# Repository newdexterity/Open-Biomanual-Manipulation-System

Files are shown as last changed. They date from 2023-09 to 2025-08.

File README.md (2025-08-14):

# The New Dexterity Open-Source Bimanual Manipulation Platform (OpenBMP) for Education and Research
Open Source Anthropomorphic Bimanual Manipulator Robot project initiated by New Dexterity

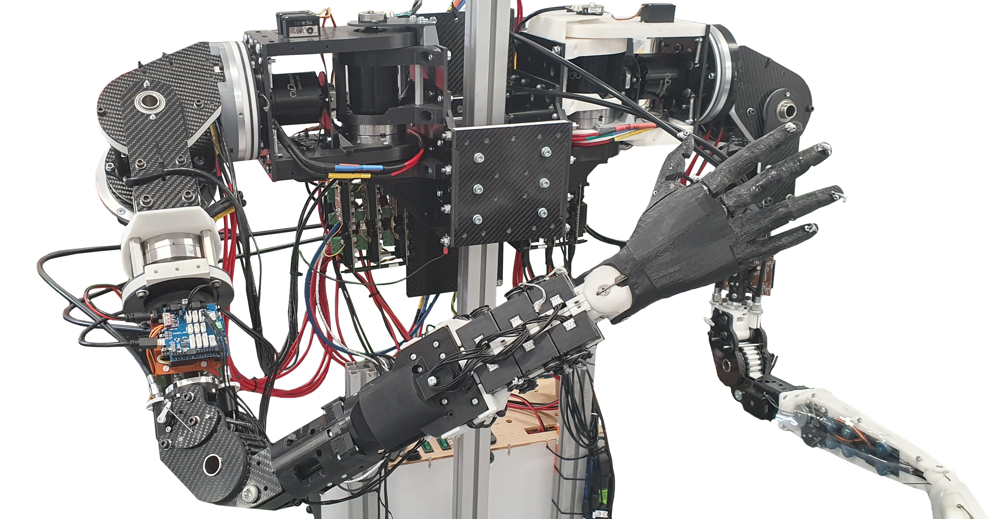
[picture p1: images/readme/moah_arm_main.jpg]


# Related Publications

[ICRA 2024 - Overview and tele-manipulation](https://www.researchgate.net/publication/380467006_The_New_Dexterity_Modular_Dexterous_Anthropomorphic_Open-Source_Bimanual_Manipulation_Platform_Combining_Adaptive_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)
[tASL paper]()

## Repository Contents
This repository contains the following material:

* Assembly guide folder - [Wiki](../../wiki)
* CAD folder - Design files of the bimanual platform for manufacturing
* Software folder - Interface for joint control - WIP (Sorting through code)

### Folder Directory
    .
    ├── ..
    ├── Assembly guide
    │   ├── Bill_of_Materials.xlsx               # Bill of Materials (WIP)        
    │   └── README.md
    ├── CAD                                      # Software folder for various subsystems
    │   ├── ...                                  
    │   ├──                                      # Various submodules of the OpenBMP system
    │   ├── ...   
    │   ├── README.md
    │   └── open_bmp_asm.7z                      # Assembled robot CAD
    ├── Software                                 # Software folder for various subsystems
    │   ├── Arduino_ESP32                        # Arduino code for operating the forearm and human-like hands for the ESP32
    │   ├── CaptoGloveDocker                     # Captoglove Docker scripts for installing and interfacing with ROS (Bluetooth)
    │   ├── Odrive_Settings                      # ODrive sample settings for setting up the ODrives (WIP)
    │   ├── moah_src                             # Main package for simulation, visualization, and operation of the robot
    │   ├── pi_catkin_ws_src                     # Code for the RPi4 CAN passover module and setup of the RPi4 for multimachine ROS
    │   │   ├── config.txt                       # RPi4 config for SPI bridge to CANBUS controller
    │   │   ├── syscfg.txt                       # RPi4 config for SPI bridge to CANBUS controller
    │   │   └── usercfg.txt                      # RPi4 config for SPI bridge to CANBUS controller and hdmi output settings
    │   ├── README.md                            # *** Overview readme file ***
    │   └── Screenshot 2023-10-12 15_46_23.png
    ├── LICENSE
    └── README.md

# About the Modular Open-source Arm Hand (MOAH) Hybrid-drive Bimanual Arm Hand System
## The Mission

The modular, dexterous, anthropomorphic Open-source Bimanual Manipulation Platform (OpenBMP) is a collaborative open-source robot manipulator project initiated by the New Dexterity group aimed to provide a low-cost research platform for studying bimanual manipulator systems and experimental actuating systems or kinematic configurations. It follows the footsteps of ARoA, a humanoid Autonomous Robotic Assistant.

OpenBMP consists of two Modular Open-source Arm Hand (MOAH) manipulators, a single-arm manipulator system designed for simple fabrication and catering to different end effectors and forearm modules.

## System Overview
The system utilizes rapid prototyping technologies such as FDM printing and waterjet cutting to manufacture robust custom parts through carbon fiber plate-reinforced 

The bimanual platform is equipped with a pair of modular, 5 DoF upper, mixed-drive manipulators with four axially driven joints and one tendon-driven joint in each arm. A 1:100 reduction harmonic drive from HanZhen Technology was used in each direct axial drive joint, enabling standard connectors between the various modules. The Bowden cable tendon-driven elbows allow the actuating mechanism to be placed away from the joint, reducing the arm's inertial moments. Each upper arm shoulder unit joint is driven by a dual shaft brushless DC (BLDC) motor, the D6374-150KV, from ODrive robotics. The position feedback employs absolute encoders, AMT232B-V from CUI Devices, to provide compact, accurate, and fast position controls. The torso structure was designed to be mounted on a pair of opposing linear rails to access a larger reachable workspace similar to the variable torso of the New Dexterity ARoA humanoid. 

* Lightweight and reconfigurable structure
* Bowden drive joints
* Box-style structure for easy access and maintenance
* Open-source ODrive Controllers for BLDC motors

## Robot Hardware Overview

### Foldable Shoulder
The foldable shoulder enables re-orientation of the manipulator bases, allowing for a larger intersecting bimanual workspace. This demonstrates how the modular platform can be modified for different kinematic designs through different actuator orientations. With detachable modules and 3D-printed sandwiched plate structures, the layout of the system can be quickly reconfigured. For example, a raised shoulder abduction module can be used to fit different types of robotic configurations and designs. 

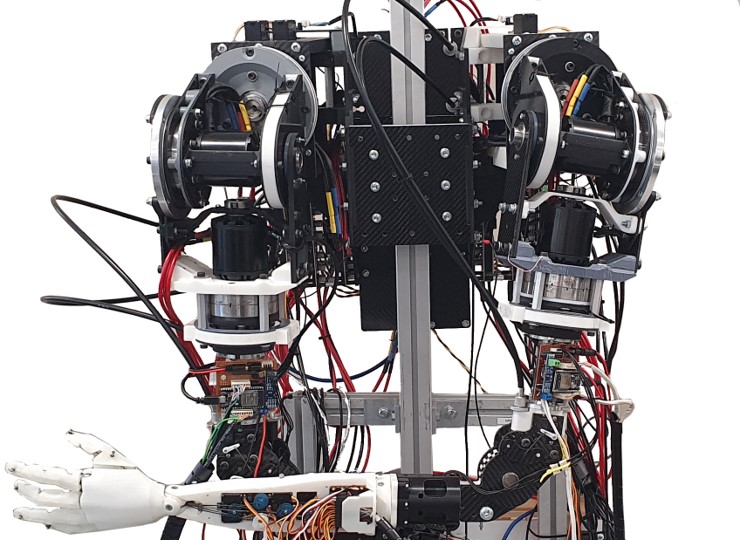
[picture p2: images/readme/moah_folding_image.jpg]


### Joint Locking
A specialized joint locking mechanism is used in both the shoulder and elbow flexion joints, mitigating motor stress during high-load manipulation tasks such as holding extended poses for long periods. The ratchet lock systems employed enable the joints to maintain their position with minimal energy expenditure, thereby reducing the overall torque exerted on the motors. The curved design also allows gravity-assisted locking modifications for future iterations.
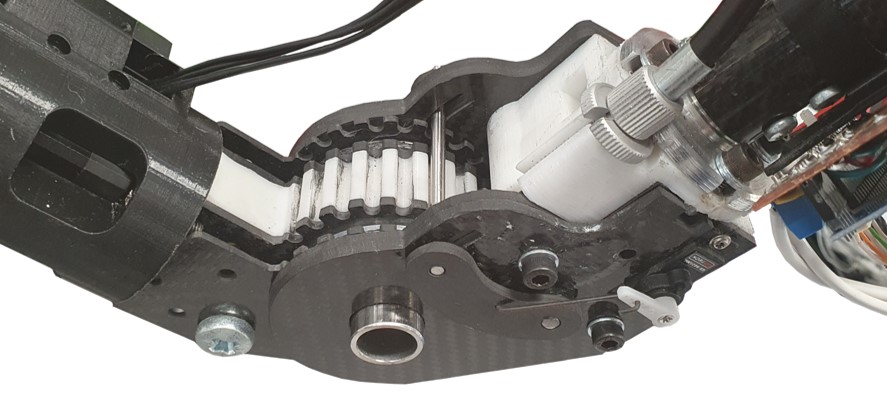
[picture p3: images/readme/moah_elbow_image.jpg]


### Low-inertial Manipulators and Experimental Transmissions
The system incorporates two types of reducer transmission mechanisms that were used to demonstrate the versatility and capability of the platform. One is a directly coupled tendon drive onto the harmonic drive output with a total reduction of approximately 61.17. The other is a simple pulley system routed around central idler wheels for the compactness of a single-joint drive. The pulley system consists of an antagonistic 1:6 reduction pulley set with an output tendon driver reduction of 2.6. The total reduction is approximately 15.6. Both transmission systems use Bowden cables to route the tendons to the elbow joint and are fitted with in-line cable tensioners. The design enables easy exchange or modification of the elbow module without disassembling the shoulder modules and also allows for the replacement of Bowden cable sets through slotted in-line cable tensioners without requiring disassembly of the robot. 

## The Design

The torso and bi-manual upper arm unit were constructed using 3D printed polylactic acid (PLA) high-strength filament parts, which were reinforced with carbon fibre composite plates in regions subjected to high loads. This choice of materials enables rapid prototyping and facilitates easy design modifications via Fused Deposition Modeling (FDM) 3D printing and waterjet cutting. The rigidity of the carbon fibre plates prevents structural deformation of the PLA parts, and the conductive nature provides grounding planes in the chassis. Additionally, certain modules were structurally reinforced using aluminium standoffs, and a machined keyed shaft adapter drove each motor-harmonic drive module.

Here is an overview of the structural parts required for assembling the torso and one of the upper arm units:
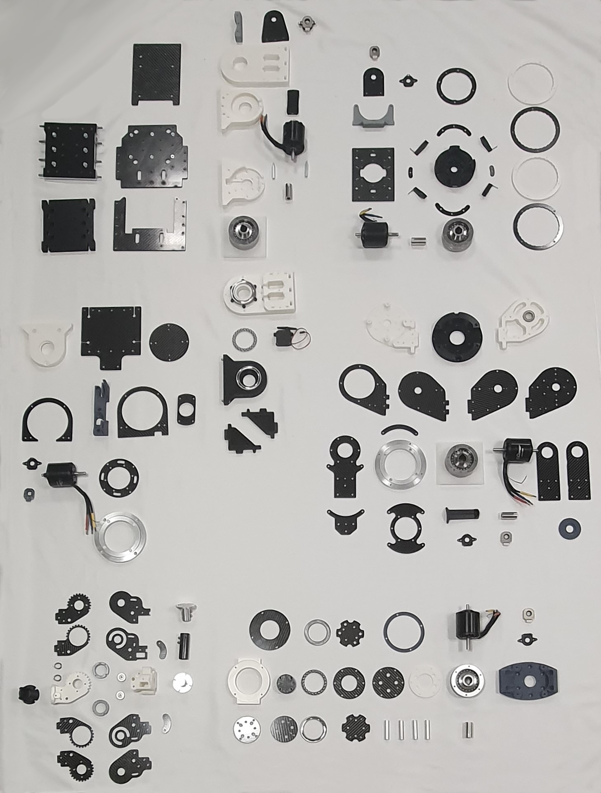
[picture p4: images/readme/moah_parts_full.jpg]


### Torso Base Unit
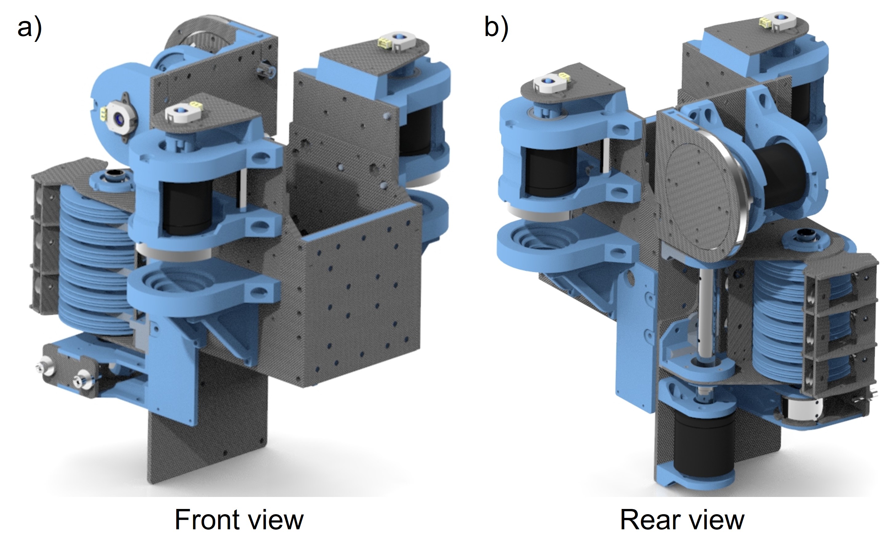
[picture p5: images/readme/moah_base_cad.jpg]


### Torso Clavicle Unit
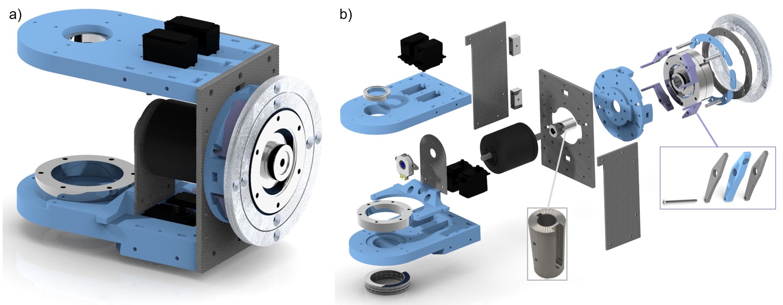
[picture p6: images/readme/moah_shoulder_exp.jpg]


### Shoulder Unit
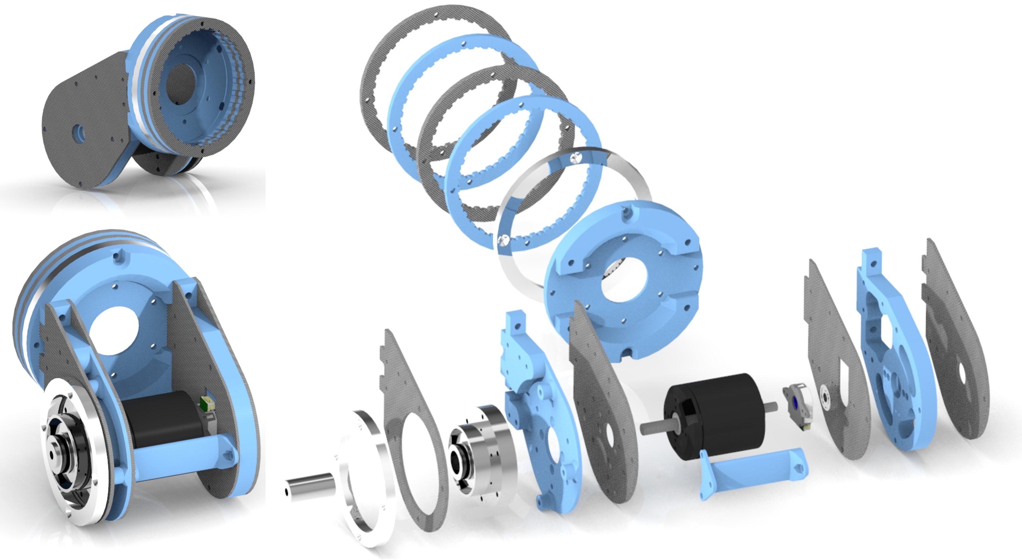
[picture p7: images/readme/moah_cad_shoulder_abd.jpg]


### Shoulder Rotation Unit
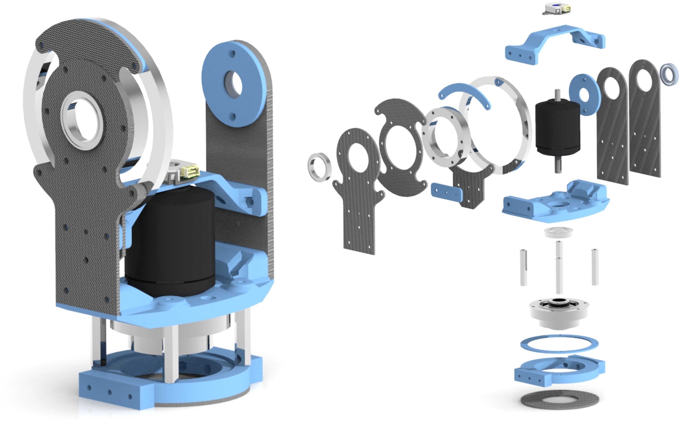
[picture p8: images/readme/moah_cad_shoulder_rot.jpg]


### Elbow Unit
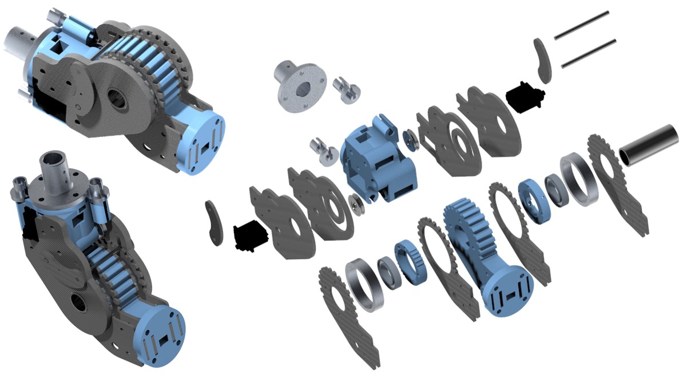
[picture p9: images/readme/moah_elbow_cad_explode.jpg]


### Forearm Modules
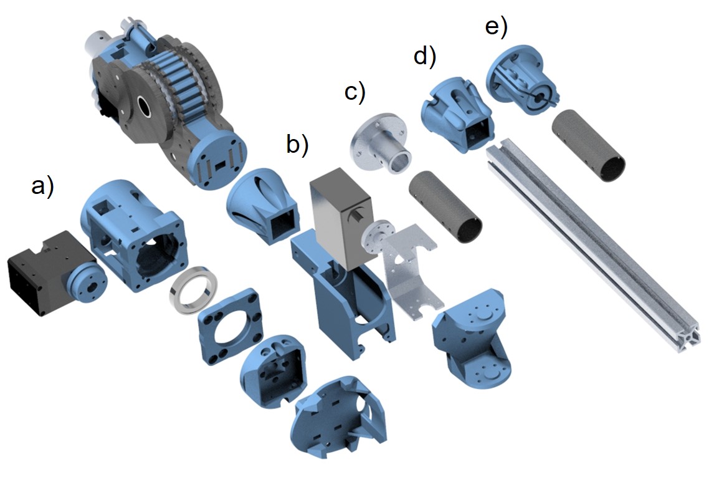
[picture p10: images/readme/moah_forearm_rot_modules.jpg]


### Wrist/Hand Modules
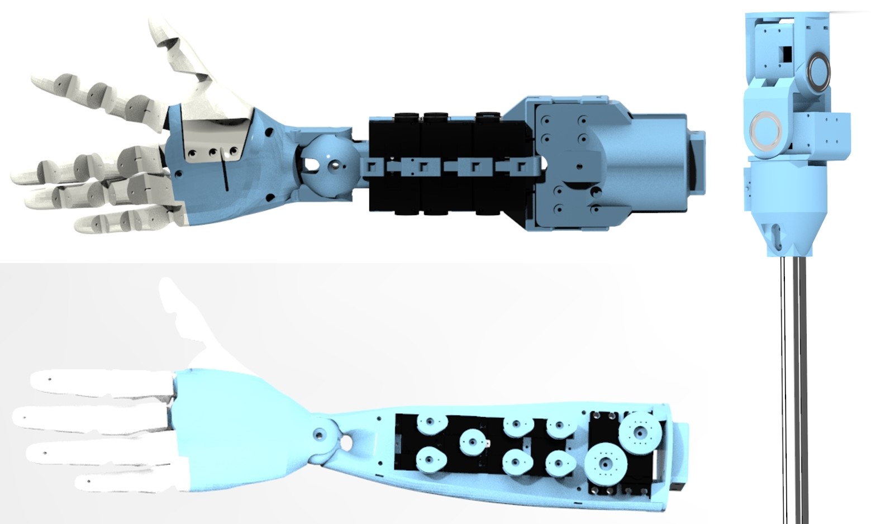
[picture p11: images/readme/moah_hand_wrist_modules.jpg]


## Robot Manipulator specifications
* Reachable arm length: 1000 mm
* Single arm weight: 12.4 kg 
* Software requirements: ROS Melodic/Noetic
* Multimachine communication: Ethernet via router
* CAN bus communication: CANbus hat via SPI with RPi4 using ROS noetic for arm64
  
### Hardware costs (approximate) (USD):
>    ### Bimanual robot arm platform (without forearm module):
>         $11600
>    ### Single ASL hand (servo Ver.)
>         $450
>    ### Single Dynamixel hand
>         $1920
>    ### Single unit of robotic wrist module
>         $1230

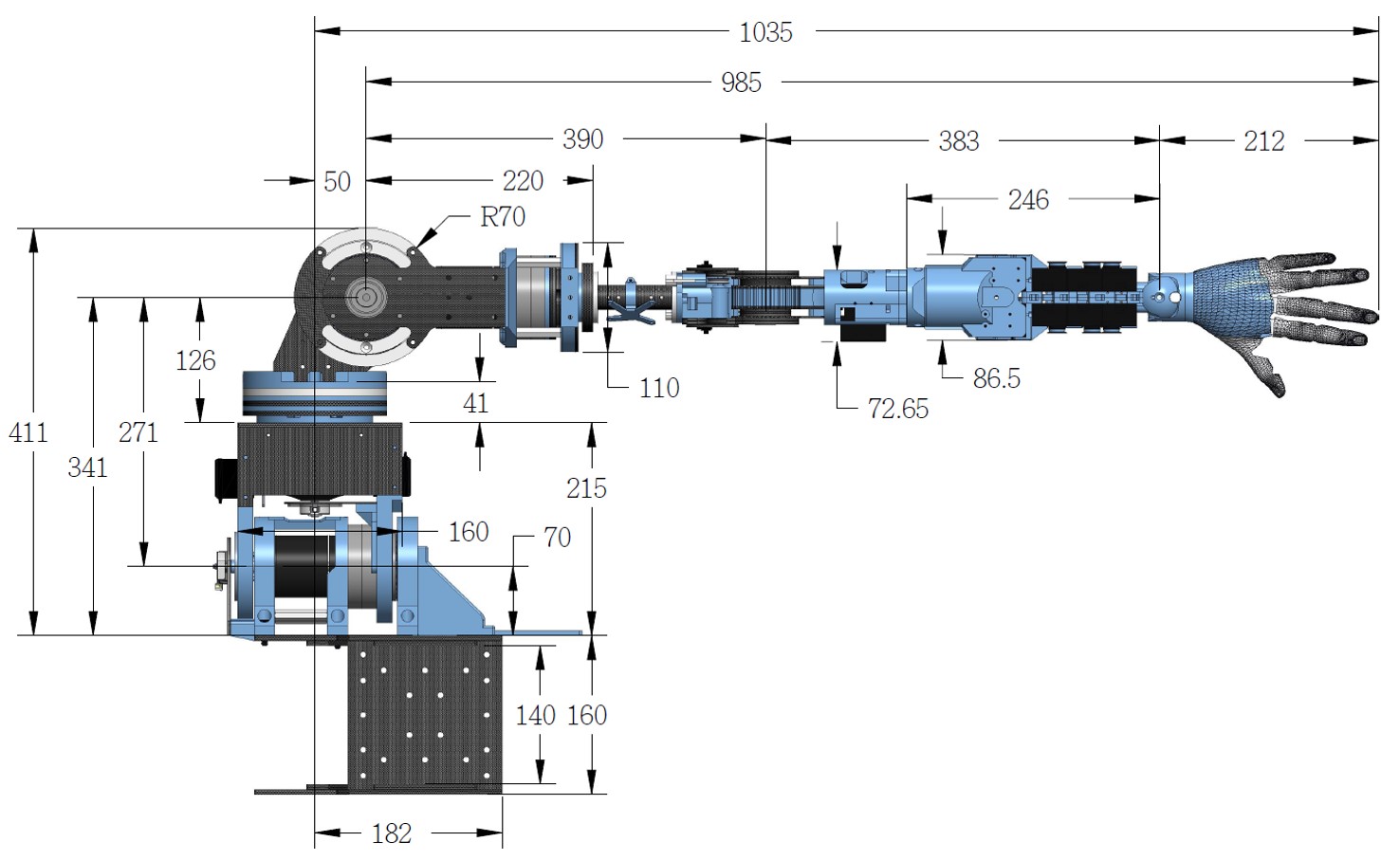
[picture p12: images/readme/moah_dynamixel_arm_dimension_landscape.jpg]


### Theoretical capabilities:
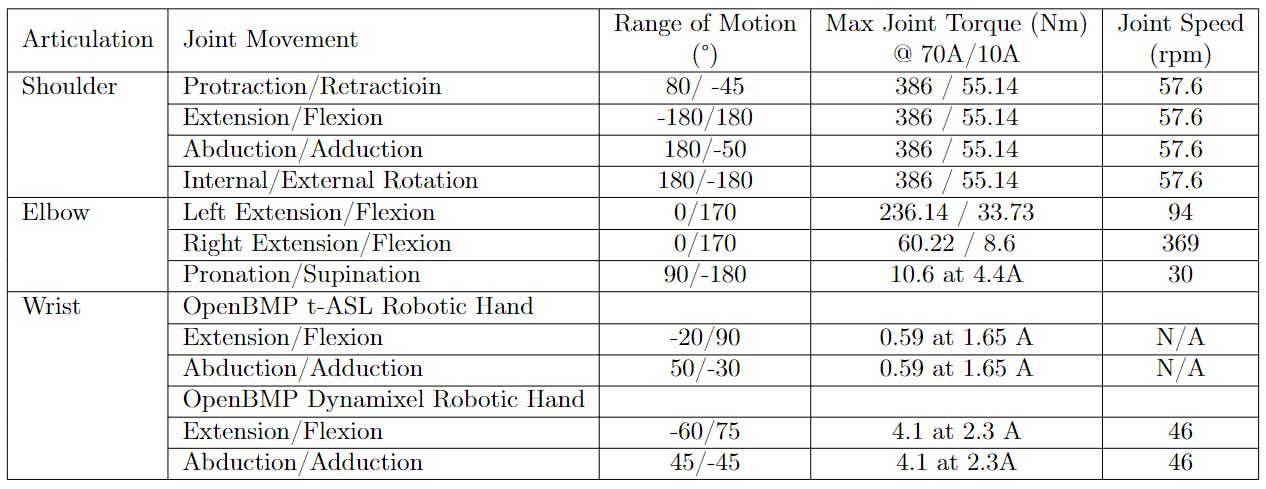
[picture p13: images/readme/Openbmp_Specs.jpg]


## Computer and Electronics

* Robot CAN controller node: Raspberry Pi 4 Model B with custom MCP2515 CAN controller and MCP2551 CAN transceiver hat
* Main Computer: Intel NUCi7 or similar with Ubuntu 18.04 with ROS melodic - 20.04 noetic should work
* Router: TP-link Archer VR300 (any router would do)
* Power supplies: assorted 6V, 12V, 24V or 48V power supplies
* Microcontrollers: ESP32 boards for ROS control for forearms and hands
* MAX485 transceiver boards for RS485 communication with Dynamixel motors
* Vero boards for custom interfacing
* Tri-state buffer (74AHC1G125S) for AMT232 SPI communication with ODrive
* Old Ethernet cables for signal wiring
* Assorted cables for power wiring

## Teleoperation
The robot can accept a variety of input controls via the ROS framework. The base system demonstrates the integration of different telemanipulation controllers with the Captoglove and the Polhemus magnetic system.

## Power Distribution System - WIP
The 56V ODrive controllers can operate motors with voltages up to 56V and peak currents of 120A per motor. However, for continuous operation, it is recommended to operate at a much lower current.

Heatsink only in still air: 40A
Heatsink with basic fan cooling: 75A
Heatsink with overkill fan cooling: 90A

Retrieved from :
[Details](https://discourse.odriverobotics.com/t/odrive-mosfet-temperature-rise-measurements-using-the-onboard-thermistor/972)

The base system limits current supply at 10A and voltage at 24V for safety in testing and operation. A higher current and voltage bypass is possible via the optional 48V battery pack. 
Here's a link to a nice article on power source selection:
[Details for custom powersources](https://things-in-motion.blogspot.com/2018/12/how-to-select-right-power-source-for.html)

## Endpoint Traverse Speed - WIP
The motors were limited to 60rpm on the ODrive controller, which is roughly 6 rpm after the harmonic reducers. Using the DH parameter and Jacobian, the end traverse speed is about 0.27m/s.
This was both a structural safety precaution as well as the power system limit. However, from experiments, the system did reach speeds of 0.36m/s during motion replication tasks.
If we use the theoretical max speed per joint, of 57.6 rpm, this computes to about 2.59m/s. The system has not been stress-tested at this kind of speed!

https://github.com/adam-p/markdown-here/wiki/Markdown-Cheatsheet

https://github.com/orgs/community/discussions/16925

<p align="justify"> The project is distributed under the Creative Commons Attribution-NonCommercial 4.0 International (CC BY-NC 4.0) </p>

[CC BY-NC 4.0](https://creativecommons.org/licenses/by-nc/4.0/)

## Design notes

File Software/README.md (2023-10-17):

# Software:
All the software needed to run MOAH is organized in this folder.

# WIP:

- [ ] Organize the code
- [ ] Replicate the code in a fresh system
- [ ] Implement low-level CAN-Bus communication directly from the ROS Control driver

<!---
# RIS for RPi4
Please follow the link to install ROS-noetic on RPi4. Steps for custom configurations such as boot-previlages, network settings, SPI settings, and setup of the RPI4 is currently a WIP.

# moah_ws

Example ROS interface to control the bimanual manipulator system. Modular, Open-source Arm Hand (MOAH) system was the old project name.
This includes the simulation and operation of the robot in rViz.

## Dependencies

# CaptoGloveDocker

The Bluetooth communication is set within a docker and can be installed following the steps listed below :

* WIP

## Setting Up ODrive Controllers
Please make sure to go through [getting started](https://docs.odriverobotics.com/v/0.5.6/getting-started.html) page for setting up and tuning the ODrive motors
A set of basic initial settings is avaliable for the ODrives

### Setting commands and motor numbering

## System Networking

You will need some ethernet cables, a router, a computer (our case was the NUC7), and a RPi4. 

### Main Computer (with moah_ws)

```
ROS_MASTER =
```

```
ROS_IP =
 ```
### RPi4 ROS to CANbus Passover

```ROS_MASTER = ```
```ROS_IP = ```

## Virtual Interface Usage
### On the Main Computer (with moah_ws)
* ToDo - add a screenshot of the terminator split screen
First start rescore

```
roscore
```

Then, run the following command to bring up the visualizer.

```
roslaunch
```

If you wish to test the robot model, edit the `view_arm.launch` files and uncomment the GUI controls for slider control of the robot arms

To bringup the controllers, run the following

```
roslaunch
```

To start the motion remapping via functional anthropomorphism, run the following commands to start the controller for each of the arms.

```
roslaunch
```

```
roslaunch
```

### Connection to Input Interfaces
The robot system is designed for the hybrid glove setup with individual controls for the hand and arm. 
The Captoglove bluetooth interface is setup within a Dockerfile. 

If the Captoglove is not showing blue, (most likely orange or magneta) press and hold the button until an orange light flashes after the light turns off (approx, 9 secs). This should set the captoglove into a white light indicator for it to be in pairing mode.

change your directory to the installed docker folder
```
cd CaptoGloveDocker
```

start docker

```
./start melodic_11
```

make sure dbus connection is successful

#### Connecting Captoglove
```
bluetoothctl
```

```
scan on
```

Once the MAC address and captoglove appears, stop the scan and connect to the glove
```
scan off
```

```
connect XX:XX:XX:XX:XX
```

Remember to pair the device before exiting bluetoothctl
```
pair
```

```
exit
```

Now run the captoglove wrapper. The finger flexion positions are published to `\leftservo_recorded` topic
```
roslaunch
```

To start the Polhemus, please use the provided package and run the following command.
NOTE : For calibration purposes, only turn on the Polhemus machine once the user wearing the sensor is in the initial position. Once the liberty system indication light turns green, run the following command to start the Polhemus system.

```
roslaunch
```

Once the markers are found, you should see the markers published under `\tf` in RViz

## Connecting to Physical Robot
On the RPi4, once multi-machine ROS is setup, run the following command to start passing the commands from the topics `\leftarm\position_controller\command` and `\rightarm\position_controller\command` over onto the CANbus network where the ODrive boards will try to move to the target positions.

```
rosrun
```

For faster communications, remember to change the `txqlen` to 1 for the can interface

```
sudo ip .....
```
-->

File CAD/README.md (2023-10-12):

# 3D Models

The provided file format for the parts in STEP.
Some of the commercially available, off-the-shelf parts have simplified geometries for rendering.

# File Structure

The assembled step file can be found in open_bmp_asm.7z. The current version is a place holder with the old part naming system. Each of the modules has their own folder.

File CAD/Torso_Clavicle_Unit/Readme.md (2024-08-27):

# Torso Clavicle Unit

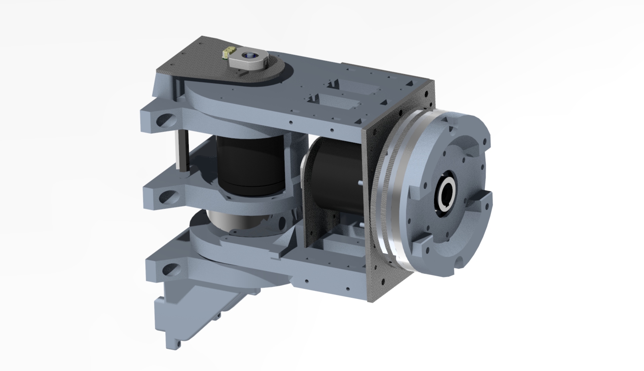
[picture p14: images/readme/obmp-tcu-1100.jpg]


The torso clavicle unit houses two motors responsible for shoulder bending and shoulder flexion. The clavicle arms can be reinforced with carbon fibre plates to prevent plastic buckling.
The unit also comes with a detachable shoulder flexion mounting unit. The flexion mounting also has a tendon-driven locking ratchet mechanism which can be made from sandwiched parts.

# Parts Needed (left arm)
## 3D Printed

* 1 X OBMP-TCU-1110
* 2 X OBMP-TCU-1120
* 1 X OBMP-TCU-1121
* 1 X OBMP-TCU-1130
* 1 X OBMP-TCU-1140
* 1 X OBMP-TCU-1141
* 1 X OBMP-TCU-1143
* 1 X OBMP-TCU-1150
* 1 X OBMP-TCU-1155 (Alternative sensor stand)
* 1 X OBMP-TCU-1160
* OBMP-TCU-1160-S (Solid version without servo mounting)
* 1 X OBMP-TCU-1161
* 1 X OBMP-TCU-1170
* OBMP-TCU-1170-S (Solid version without servo mounting)
* 1 X OBMP-TCU-1180
* 1 X OBMP-TCU-1183
* 2 X OBMP-TCU-1185 (locking ring)
* 1 X OBMP-TCU-1186 (flexion arm mounting)
* 4 X OBMP-TCU-1189 (ratchet core)

## Carbon Fiber Sheets
### 5 mm thick

* 1 X OBMP-TCU-P5-1171
* 2 X OBMP-TCU-P5-1185 (locking ring)

### 3 mm thick

* 1 X OBMP-TCU-P3-1151
* 1 X OBMP-TCU-P3-1184
* 8 X OBMP-TCU-P3-1188
* 2 X OBMP-TCU-P3-1163 (optional side panels

### 2 mm thick

* 1 X OBMP-TCU-P3-1162

## Mechanical parts

* 2 X OBMP-MOTOR-COUPLER (Machined motor coupler)
* 2 X XB3-B-60-100 Harmonic drive
* 2 X 6x6x20 mm Machine key
* 2 X M5X51 mm Aluminium standoff
* 1 X ASL140-085 Aluminium bearing
* 1 X SKF 51110 thrust bearing
* 3 X 6806ZZ bearing
* 4 X M6X32 mm dowel pins (or longer)
* 4 X M2X40 mm screw (or longer)
* 7 X M6X20 mm Hex screws
* 14 X M5X16 mm Hex screws
* 10 X M4 Bolts (support alignment bolts for holding the plates in place)
* Assorted M6, M5, and M4 Nuts

## Motors and Sensors

* 2 X D6374-150KV
* 2 X CUI AMT232V (can swap for other compatible AMT sensors)

# Parts Needed (Right arm)
## 3D Printed

* 1 X OBMP-TCU-1121 (mirrored) (odrive stack base)

## Rest of parts are same for both arms

# Notes
## Motor Spacer (obmp-tcu-1143)

This part requires heat inserts for reliable connection of the plates. Alternatively, a slot could be cut for inserting a nut instead.

## Ratchets (obmp-tcu-1181 & obmp-tcu-1182)

obmp-tcu-1182 is the mirrored version of obmp-tcu-1181. When building, the mirrored parts can be made by changing the install orientation of the M2 screw.
The ratchets can be assembled using obmp-tcu-1189 and two pieces of obmp-tcu-p3-1188. The lever arm is made of a M2x40 mm screw.

## Machined part (obmp-tcu-1190)

The motor-harmonic drive coupler using the 6x6 mm square key and the stock 3 mm key that comes with the D6374-150KV motor can be subjected to very high torsional forces.
Hence, it is required to be one of the few parts that needs to be properly machined out of steel. The original parts were machined out of 316 stainless steel. A workshop-ready part drawing is provided.

## Alternative Sensor Mounting (obmp-tcu-1150)

Instead of the two piece mount, a fully 3d printed version can be used instead (obmp-tcu-1155)

## Absolute Output Sensing (obmp-tcu-1149)

The part obmp-tcu-1149 is designed for direct joint angle sensing for the shoulder rotation axis. This is an optional part as the current system relies on the low backlash harmonic drives to perform correctly.

## Odrive Mounting Plate (obmp-tcu-1121)

Remember to mirror this part for the opposite arm

## ToDo

Update obmp-tcu-1160 to have 3mm carbon plates

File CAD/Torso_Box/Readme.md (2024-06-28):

# Torso Box Base

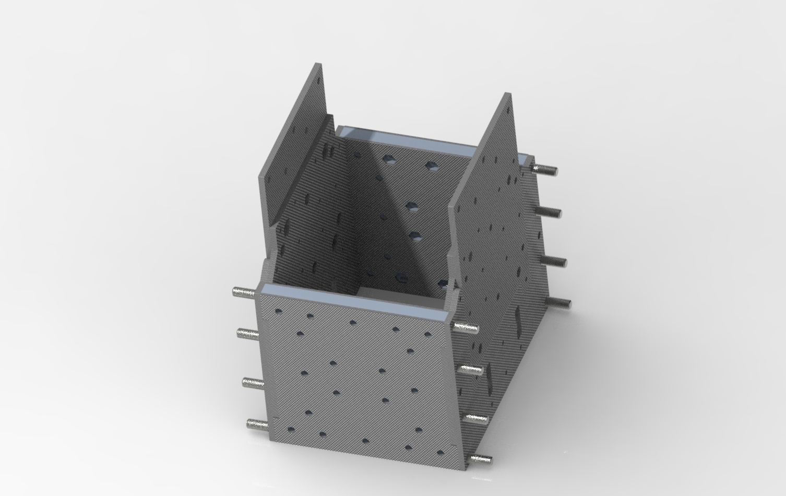
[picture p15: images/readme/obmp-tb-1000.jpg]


The torso base is a simple box designed to enclose around a pair of linear rails. The sandwhiched plates allows an assortment of attachement points for different systems.
Using two layers of 5 mm thich carbon fiber boards, the box structure is connected by M8 threaded rods to provide the mounting point for the robot arms and transmission mechanisms

# Parts Needed
## 3D Printed

* 2 X OBMP-TB-1010

## Carbon Fiber Sheets

* 2 X OBMP-TB-P-1010
* 2 X OBMP-TB-P-1011
* 2 X OBMP-TB-P-1020
* 2 X OBMP-TB-P-1021
* 2 X OBMP-TB-P-1022

## Mechanical parts

* 8 X OBMP-TB-1011 (M6 threaded rod, 200 mm lengths)
* 16 X M6 Washers
* 36 X M6 Nuts (go on the inside of the plates)
* 10 X M4 Bolts (support alignment bolts for holding the plates in place)
* 10 X M4 Nuts

# Notes
## M8 Threaded Rod

The threaded rods in the CAD is 200 mm long. This can be shortened to 170 mm or 180 mm, just save enough space for the washer and nut to go on.
The threaded rods runs the length of the 3d printed obmp-tb-1010 part, this can be easily assembled by taking the threaded rod held in a cordless drill and drill the rods into the plastic part like a threading tap.

## M6 Connectors

The front plate, obmp-tb-1010 and the associated carbon fiber plates are connected to the base frame via 6xM6 mounting point on each side. 
For mounting on the simple base stand, use a 20x20 mm aluminium extrusion to create an intersecting structure to attach to the verticle structure of the base stand.

## Carbon Fiber

The parts with P-xxxx means plates for carbon fiber parts, the thickness used for the torso base are 5 mm and 2 mm sheets.

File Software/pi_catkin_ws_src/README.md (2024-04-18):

# Code for the RPi4 CAN passover

- [ ] Implement C++ version of CAN bus communication with ROS
- [ ] Improve control loop time

## Usage

Download and extract `moa_odrv_ros` folder to `catkin_ws/src/` on your RPi4
run catkin_make on your RPi4

## Acknowledgements

Adapted from following code sources:

- [ODrive main repo](https://github.com/neomanic/odrive_ros)
- [https://github.com/belovictor](https://github.com/belovictor/odrive_can_ros_driver)

# Note:

Change txquelen to 1 for the canbus settings to prevent delayed motion.

#

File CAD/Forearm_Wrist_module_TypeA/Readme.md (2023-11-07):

# Type A Adjustable Wrist Module

This module fits the type A square quick adaptor and consists of two DoF (Wrist adduction and flexion)

# Parts Needed
## 3D Printed

* 1 X OBMP-FWM-A-1610
* 1 X OBMP-FWM-A-1620
* 1 X OBMP-FWM-A-1630
* 1 X OBMP-FWM-A-1640
* 1 X OBMP-FWM-A-1660
* 1 X OBMP-FWM-A-1670

## Mechanical Parts

* 1 X OBMP-FWM-A-1650 (25 mm diameter carbon fibre tube)
* 2 X 6805ZZ bearing

## Motors and Sensors

* 1 X XM540-W270-R
* 1 X XM430-W350-R
  
# Notes

This is an alternative wrist module with 2 DoF. Compatible with the 25 mm carbon fibre tube forearm adaptors.

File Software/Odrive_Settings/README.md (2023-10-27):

# Basic ODrive board settings

* Its a good idea to keep a record of the serial number of which board is what.
* R means right arm, L means left arm
* R1 is torso-shoulder bending and shoulde flexion motor
* R2 is shoulder abduction and upper arm rotation
* R3 is for elbow

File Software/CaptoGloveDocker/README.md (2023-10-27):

# Resources for enabling BLTE 
https://www.jaredwolff.com/get-started-with-bluetooth-low-energy/

build the docker using 
docker build -t <image_name>:<tag_name> <dockerfile_path> 
for concrete example use
docker build -t ros_capto_img:kinetic_11 .

use this command to start docker
./start kinetic_11

## Notes
* The hci and bluetooth client channels for publishing the finger sensor data seems to be linked to the settings uploaded to the captoglove in the captoglove suite.
* ToDo: upload a copy of glove settings for this code to work
* currently the thumb pressure data and index finger data overlaps in the data extracted from the channels

once in should see :
non-network local connections being added to access control list
Using 'aroa' as username, with UID=1000 and GUID=1000
Mouting host folder '/home/aroa/CaptoGloveDocker/Melodic_11_Projects/' to '/home/aroa/' in the container
Using 'docker' to run container
 * Starting system message bus dbus                                      [ OK ] 
 * Stopping bluetooth                                                    [ OK ] 
 * Starting bluetooth                                                    [ OK ] 

use bluetoothctl to connect to captogloves
bluetoothctl
scan on
***hold down button on captoglove for 7 s, until it flashes off, then back on into white/orange. want to go into white light mode
scan off
connect D4:B9:A8:85:E2:22
connect C2:4F:2D:05:78:D9
quit

sameple:
root@ARoA-NUC:/home/developer/catkin_ws# bluetoothctl
Agent registered
[bluetooth]# scan on
Discovery started
[CHG] Controller 94:B8:6D:84:32:F7 Discovering: yes
[NEW] Device 51:39:62:52:21:79 51-39-62-52-21-79
[NEW] Device 64:96:0C:52:3A:C7 64-96-0C-52-3A-C7
[NEW] Device C2:4F:2D:05:78:D9 CaptoGlove
[bluetooth]# scan off 
Discovery stopped
[CHG] Controller 94:B8:6D:84:32:F7 Discovering: no
[CHG] Device D4:B9:A8:85:E2:22 RSSI is nil
[CHG] Device 64:96:0C:52:3A:C7 TxPower is nil
[bluetooth]# connect C2:4F:2D:05:78:D9
Attempting to connect to C2:4F:2D:05:78:D9
[CHG] Device C2:4F:2D:05:78:D9 Connected: yes
Connection successful

[CHG] Device D4:B9:A8:85:E2:22 Connected: no
[NEW] Primary Service
	/org/bluez/hci0/dev_C2_4F_2D_05_78_D9/service0008
	00001801-0000-1000-8000-00805f9b34fb
	Generic Attribute Profile
[NEW] Primary Service
	/org/bluez/hci0/dev_C2_4F_2D_05_78_D9/service0034
	0000180a-0000-1000-8000-00805f9b34fb
	Device Information
[NEW] Characteristic
	/org/bluez/hci0/dev_C2_4F_2D_05_78_D9/service0034/char0035
	00002a50-0000-1000-8000-00805f9b34fb
	PnP ID
[NEW] Primary Service
	/org/bluez/hci0/dev_C2_4F_2D_05_78_D9/service0037
	0000ff05-3333-acda-0000-ff522ee73921
	Vendor specific
[NEW] Characteristic
	/org/bluez/hci0/dev_C2_4F_2D_05_78_D9/service0037/char0038
	0000f001-3333-acda-0000-ff522ee73921
	Vendor specific
[NEW] Characteristic
	/org/bluez/hci0/dev_C2_4F_2D_05_78_D9/service0037/char003a
	0000f002-3333-acda-0000-ff522ee73921
	Vendor specific
[NEW] Descriptor
	/org/bluez/hci0/dev_C2_4F_2D_05_78_D9/service0037/char003a/desc003c
	00002902-0000-1000-8000-00805f9b34fb
	Client Characteristic Configuration
[NEW] Characteristic
	/org/bluez/hci0/dev_C2_4F_2D_05_78_D9/service0037/char003d
	0000f003-3333-acda-0000-ff522ee73921
	Vendor specific
[NEW] Descriptor
	/org/bluez/hci0/dev_C2_4F_2D_05_78_D9/service0037/char003d/desc003f
	00002902-0000-1000-8000-00805f9b34fb
	Client Characteristic Configuration
[NEW] Characteristic
	/org/bluez/hci0/dev_C2_4F_2D_05_78_D9/service0037/char0040
	0000f004-3333-acda-0000-ff522ee73921
	Vendor specific
[NEW] Descriptor
	/org/bluez/hci0/dev_C2_4F_2D_05_78_D9/service0037/char0040/desc0042
	00002902-0000-1000-8000-00805f9b34fb
	Client Characteristic Configuration

roslaunch captoglove_ros_wrapper captoglove_ros_wrapper.launch

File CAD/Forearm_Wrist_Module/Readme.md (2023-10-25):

# XM540 Wrist Module

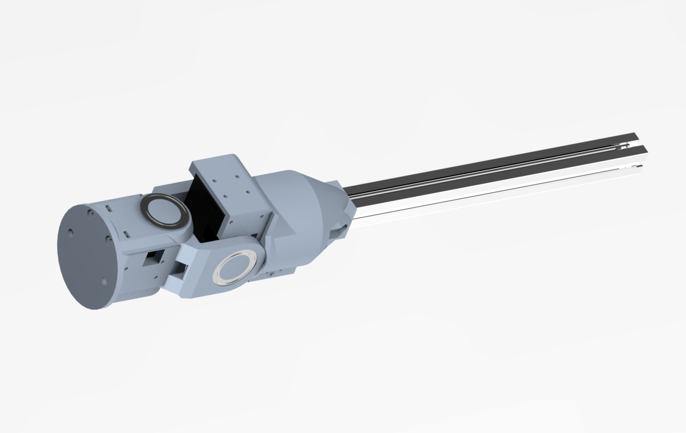
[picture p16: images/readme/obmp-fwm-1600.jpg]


A wrist module compatible with Type B and Type D forearm adaptors. The end connector is designed for dovetail adaptor plates for mounting various grippers.

# Parts Needed (left arm)
## 3D Printed

* 1 X OBMP-FWM-1610
* 1 X OBMP-FWM-1620
* 1 X OBMP-FWM-1630
* 1 X OBMP-FWM-1640
* 1 X OBMP-FWM-1650
* 1 X OBMP-FWM-1660
* 1 X OBMP-FWM-1670

## Mechanical Parts

* 1 X F6806ZZ flanged bearing
* 1 X OBMP-FWM-1680 (Adjustable aluminium extrusion)
* 2 X 6805ZZ bearing

## Motors and Sensors

* 2 X XM540-W270-R
* 1 X XM430-W350-R
  
# Notes

This is a stand-alone wrist module with 3 DoF. Compatible with the 22 mm X 22 mm aluminium extrusion forearm adaptors.

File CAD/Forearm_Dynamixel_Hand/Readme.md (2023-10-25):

# Forearm Dynamixel Hand (Right Hand)

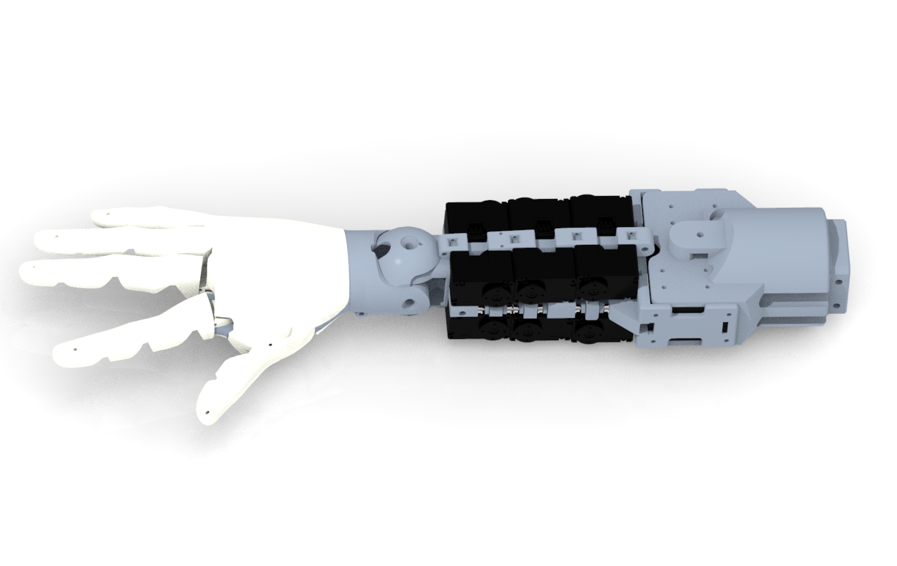
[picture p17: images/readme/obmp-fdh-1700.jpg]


# Parts Needed (right hand)
## 3D Printed

* 1 X OBMP-FDH-1710
* 2 X OBMP-FDH-1720
* 1 X OBMP-FDH-1730
* 1 X OBMP-FDH-1751
* 1 X OBMP-FDH-1752
* 1 X OBMP-FDH-1754
* 4 X OBMP-FDH-1758
* 12 X OBMP-FDH-1760

## 3D Printed with Flexible filament (NinjaFlex)

* 1 X OBMP-FDH-1753
* 1 X OBMP-FDH-1755
* 1 X OBMP-FDH-1756
* 1 X OBMP-FDH-1757

## Mechanical parts

* 2 X OBMP-FDH-1740
* 12 X MF52ZZ flanged bearing
* 24 X MR52ZZ bearing

## Motors

* 12 X XC330-M288-T
* 2 X XM430-W350-T

# Notes

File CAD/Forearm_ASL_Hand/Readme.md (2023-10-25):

# Forearm ASL Hand (left hand)

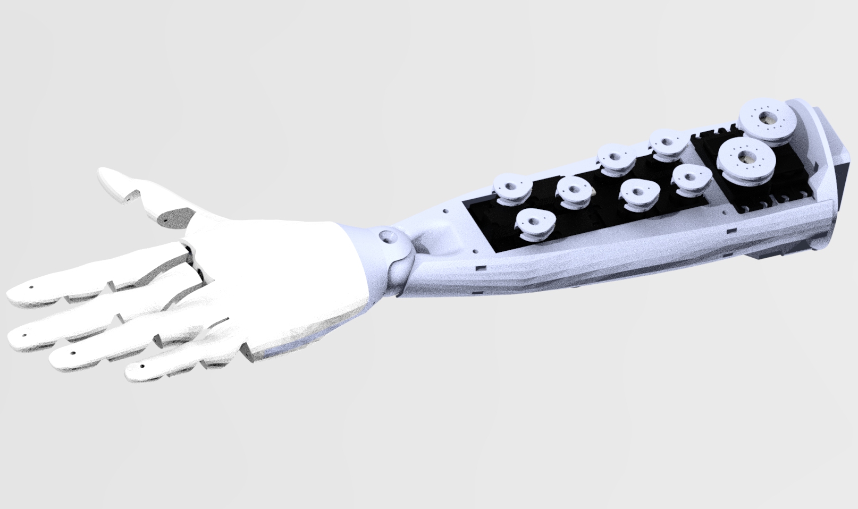
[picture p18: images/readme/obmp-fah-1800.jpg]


# Parts Needed (left hand)
## 3D Printed

* 1 X OBMP-FAH-1810
* 1 X OBMP-FAH-1811 (Optional)
* 1 X OBMP-FAH-1820
* 1 X OBMP-FAH-1830
* 2 X OBMP-FAH-1840
* 2 X OBMP-FAH-1841
* 10 X OBMP-FAH-1842
* 1 X OBMP-FAH-1851
* 1 X OBMP-FAH-1856
* 1 X OBMP-FAH-1857
* 4 X OBMP-FAH-1858

## 3D Printed with Flexible filament (NinjaFlex)

* 1 X OBMP-FAH-1852
* 1 X OBMP-FAH-1853
* 1 X OBMP-FAH-1854
* 1 X OBMP-FAH-1855

## Motors

* 2 X FS5115 Servo
* 12 X GS-9025MG Servo

# Notes

* 1 mm dyneema cables were used as tendons.
* 9g servo horns were cut and attached to the horns with heated pins or via glue.
* 5115 servo horns can be attached via cable termination.
* For connecting with Type B forearm connector, swap out OBMP-FAH-1810 with OBMP-FAH-1811

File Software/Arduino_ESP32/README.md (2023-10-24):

# Arduino code for ESP32 NODEMCU boards controlling the ASL forearm unit

## Requirements

* Dynamixel2Arduino
* SoftwareSerial
* ROSSERIAL
* ESP32 servo library

## Notes

Software serial for dynamixel - for rs485, remember to change Hardwareserial to softwareserial in the library

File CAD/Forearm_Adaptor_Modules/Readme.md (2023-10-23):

# Forearm Adaptors

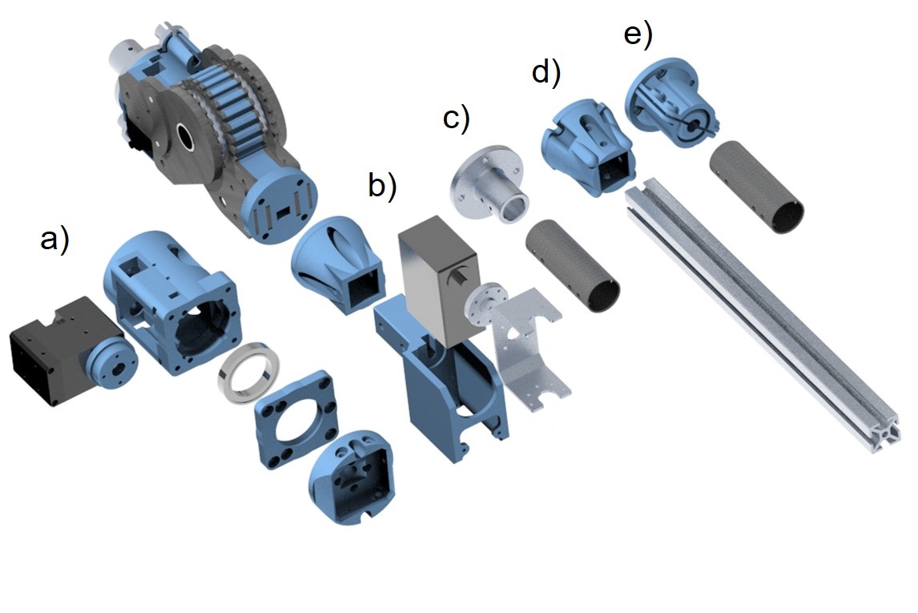
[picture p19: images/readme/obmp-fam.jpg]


Type A and Type B are motorized adaptor options. Type C and Type E are adaptors for 25 mm dia. carbon fibre tube connectors with machined or printed options. Type D is a reinforced printed connector alternative to the Type B connector for 2020 aluminium extrusions.
# Parts Needed (TypeA)
## 3D Printed
* 1 X OBMP-FAM-A-1410
* 1 X OBMP-FAM-A-1420
* 1 X OBMP-FAM-A-1430
* 1 X OBMP-FAM-A-1440
 
## Mechanical parts

* 1 X 6806ZZ bearing
 
## Motors

* 1 X XH540-W270-T

# Parts Needed (TypeB)
## 3D Printed
* 1 X OBMP-FAM-B-1410
* 1 X OBMP-FAM-B-1420
  
## Motors

* 1 X RDS5160 Servo

# Parts Needed (TypeC)
## Mechanical Part
* 1 X OBMP-FAM-C-1400 (Machined)

# Parts Needed (TypeD)
## 3D Printed
* 1 X OBMP-FAM-D-1400

# Parts Needed (TypeE)
## 3D Printed
* 1 X OBMP-FAM-E-1400

# Notes
 For Type A, the XM540 smart actuator TTL model can daisy chain with the XC330 hand. The RS485 model is fine as well but requires a separate RS485 communication channel

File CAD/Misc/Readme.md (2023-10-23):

# Misc parts
These are the models for the ESP32 adaptor board that control the hand and forearm units and the tube mounting for the board.

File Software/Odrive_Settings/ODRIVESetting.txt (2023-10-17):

sudo odrivetool dfu
//switch on odrive board to dfu, back to run once flashed

odrv0.axis0.motor.config.calibration_current = 20
odrv0.axis0.motor.config.current_lim = 20
odrv0.axis0.motor.config.pole_pairs = 7
odrv0.axis0.motor.config.torque_constant = 0.055133333333333333
odrv0.axis0.controller.config.vel_limit = 10
#turn/s

odrv0.axis1.motor.config.calibration_current = 20
10
odrv0.axis1.controller.config.vel_limit = 10
2
odrv0.axis1.motor.config.current_lim = 30
10
odrv0.axis1.motor.config.pole_pairs = 7
odrv0.axis1.motor.config.torque_constant = 0.055133333333333333

odrv0.config.enable_brake_resistor = True
odrv0.config.brake_resistance = 2.0

odrv0.axis0.encoder.config.mode = 256
odrv0.axis0.encoder.config.cpr = 2**14
odrv0.axis0.encoder.config.abs_spi_cs_gpio_pin = 1

odrv0.axis1.encoder.config.mode = 256
0
odrv0.axis1.encoder.config.cpr = 2**14
8192
odrv0.axis1.encoder.config.abs_spi_cs_gpio_pin = 4
1

odrv0.save_configuration()
odrv0.reboot()

odrv0.axis0.requested_state = AXIS_STATE_FULL_CALIBRATION_SEQUENCE
odrv0.axis1.requested_state = AXIS_STATE_FULL_CALIBRATION_SEQUENCE

odrv0.axis0.requested_state = AXIS_STATE_CLOSED_LOOP_CONTROL
odrv0.axis1.requested_state = AXIS_STATE_CLOSED_LOOP_CONTROL

odrv0.axis0.controller.input_pos = 0
odrv0.axis1.controller.input_pos = 0

odrv0.axis0.controller.input_pos = 5
odrv0.axis1.controller.input_pos = 5

start_liveplotter(lambda: [odrv0.axis0.encoder.pos_abs])
start_liveplotter(lambda: [odrv0.axis1.encoder.pos_abs])

start_liveplotter(lambda: [odrv0.axis0.encoder.spi_error_rate,odrv0.axis0.encoder.pos_abs])

start_liveplotter(lambda: [odrv0.axis0.motor.I_bus, odrv0.axis0.encoder.spi_error_rate])

start_liveplotter(lambda: [odrv0.axis0.encoder.spi_error_rate])
start_liveplotter(lambda: [odrv0.axis0.encoder.spi_error_rate,odrv0.axis1.encoder.spi_error_rate])

dump_errors(odrv0)
dump_errors(odrv0, True)
odrv0.clear_errors()

odrv0.axis0.controller.config.input_mode = 1

odrv0.axis0.requested_state = AXIS_STATE_FULL_CALIBRATION_SEQUENCE
odrv0.axis1.requested_state = AXIS_STATE_FULL_CALIBRATION_SEQUENCE
odrv0.axis0.motor.config.pre_calibrated = True
odrv0.axis1.motor.config.pre_calibrated = True

odrv0.axis0.encoder.config.pre_calibrated = True
odrv0.axis1.encoder.config.pre_calibrated = True

odrv0.axis0.config.startup_encoder_offset_calibration = True
odrv0.axis1.config.startup_encoder_offset_calibration = True
odrv0.axis0.config.startup_closed_loop_control = True
odrv0.axis1.config.startup_closed_loop_control = True
odrv0.save_configuration()
odrv0.reboot()

odrv0.axis0.controller.config.enable_overspeed_error = False
odrv0.axis1.controller.config.enable_overspeed_error = False

************change can heartbeat message
odrv0.axis0.requested_state = AXIS_STATE_IDLE
odrv0.axis1.requested_state = AXIS_STATE_IDLE

odrv0.axis0.config.can.encoder_rate_ms = 0
odrv0.axis1.config.can.encoder_rate_ms = 0
odrv0.axis0.config.can.heartbeat_rate_ms = 100
odrv0.axis1.config.can.heartbeat_rate_ms = 100
odrv0.save_configuration()

odrv0.axis1.controller.config.input_filter_bandwidth = 100
# [Hz]

odrv0.axis0.controller.config.pos_gain 
odrv0.axis0.controller.config.vel_gain
odrv0.axis0.controller.config.vel_integrator_gain

start_liveplotter(lambda:[odrv0.axis0.pos_vel_mapper.pos_rel, odrv0.axis0.controller.pos_setpoint])

R2A0
odrv0.config.dc_max_negative_current = -2
odrv0.config.dc_max_positive_current
odrv0.config.max_regen_current???

odrv0.axis0.motor.config.current_control_bandwidth = 2000
odrv0.axis0.encoder.config.bandwidth =2000

https://discourse.odriverobotics.com/t/spinout-on-hoverboard-motors/7645/6
(default 10, change to 50)
odrv0.axis0.controller.config.spinout_electrical_power_threshold = 50
odrv0.axis0.controller.config.spinout_mechanical_power_threshold = -50

odrv0.can.config.baud_rate = 1000000
odrv0.axis0.config.can.node_id = 1
odrv0.axis1.config.can.node_id = 2

Left arm
torso : 7
flex : 8
abd : 9
rot : 10 (0xA)
elbow : 11 (0xB)
empty : 12

Right arm
torso : 1
flex : 2
abd : 3
rot : 4
elbow : 5
empty : 6

**************************************pulley reducer slow it down*********************
*******************odrv0.axis0.motor.config.current_control_bandwidth = 500
odrv0.axis0.controller.config.input_filter_bandwidth = 2.0
odrv0.axis0.controller.config.input_mode = INPUT_MODE_POS_FILTER

odrv0.config.dc_max_negative_current = -0.001

odrv0.axis0.controller.config.input_filter_bandwidth = 0.5
odrv0.axis0.controller.config.vel_limit = 25
odrv0.axis0.trap_traj.config.vel_limit = 20

odrv0.axis0.trap_traj.config.accel_limit = 2

odrv0.axis0.trap_traj.config.decel_limit = 2

odrv0.axis0.controller.config.inertia = <Float>
odrv0.axis0.motor.config.current_lim = 20
odrv0.axis0.controller.config.vel_limit = 
odrv0.axis0.controller.config.input_mode = INPUT_MODE_TRAP_TRAJ
*********************************************************************************************
https://discourse.odriverobotics.com/t/encoder-on-a-driven-shaft-not-the-motor/2565/13
odrv0.axis0.encoder.config.mode = ENCODER_MODE_INCREMENTAL
odrv0.axis0.encoder.config.cpr = 8192
odrv0.axis0.encoder.config.calib_scan_distance = 62.8318530718
odrv0.axis0.encoder.config.calib_scan_distance = 12.566370614
odrv0.axis0.motor.config.pole_pairs = 700

start_liveplotter(lambda: [odrv0.axis0.encoder.pos_abs])
start_liveplotter(lambda: [odrv0.axis0.encoder.count_in_cpr])
******************************************************************************************
odrv0.axis0.encoder.config.mode = 256
odrv0.axis0.encoder.config.cpr = 2**14
odrv0.axis0.encoder.config.abs_spi_cs_gpio_pin = 1
odrv0.axis0.motor.config.pole_pairs = 700

odrv0.axis0.trap_traj.config.vel_limit = 8
odrv0.axis0.trap_traj.config.accel_limit =  //0.5 is the maximum acceleration in turns / sec^2
odrv0.axis0.trap_traj.config.decel_limit =  //0.5 is the maximum deceleration in turns / sec^2
odrv0.axis0.controller.config.inertia = 
odrv0.axis0.controller.config.vel_limit = 10
odrv0.axis0.controller.config.input_mode = INPUT_MODE_TRAP_TRAJ

	odrv0.axis0.controller.config.input_filter_bandwidth = 2.0
******************************************************************************************

odrv0.axis0.requested_state = AXIS_STATE_FULL_CALIBRATION_SEQUENCE

odrv0.axis1.requested_state = AXIS_STATE_FULL_CALIBRATION_SEQUENCE

odrv0.axis0.requested_state = AXIS_STATE_ENCODER_OFFSET_CALIBRATION
odrv0.axis1.requested_state = AXIS_STATE_ENCODER_OFFSET_CALIBRATION

odrv0.axis0.requested_state = AXIS_STATE_CLOSED_LOOP_CONTROL
odrv0.axis0.controller.input_pos = 0

odrv0.axis1.requested_state = AXIS_STATE_CLOSED_LOOP_CONTROL
odrv0.axis1.controller.input_pos = 0

odrv0.axis0.controller.input_pos = 0
odrv0.axis1.controller.input_pos = 0

    <axis>.controller.input_pos = <turn>
    <axis>.controller.input_vel = <turn/s>
    <axis>.controller.input_torque = <torque in Nm>

odrv0.axis1.motor.config
pre_calibrated = True (bool)
pole_pairs = 7 (int)
calibration_current = 10.0 (float)
resistance_calib_max_voltage = 10.0 (float)
phase_inductance = 2.85157e-05 (float)
phase_resistance = 0.102618 (float)
direction = -1 (int)
motor_type = 0 (int)
current_lim = 40.0 (float)
current_lim_tolerrance = 1.25 (float)
inverter_temp_limit_lower = 100.0 (float)
inverter_temp_limit_upper = 120.0 (float)
requested_current_range = 40.0 (float)
current_control_bandwidth = 1000.0 (float)

odrv0.axis0.motor.config.resistance_calib_max_voltage = 12.0
odrv0.axis0.controller.config.vel_limit = 5

odrv0.axis1.config.startup_closed_loop_control = True
odrv0.axis1.config.startup_encoder_offset_calibration = True
odrv0.axis1.config.startup_motor_calibration = True

odrv0.axis1.controller.config.control_mode = CONTROL_MODE_VELOCITY_CONTROL
odrv0.axis1.controller.input_vel = 1

odrv0.axis1.controller.config.control_mode = CONTROL_MODE_TORQUE_CONTROL
odrv0.axis1.motor.config.torque_constant = 8.23 / 150
odrv0.axis1.controller.input_torque = 0.1

start_liveplotter(lambda: [odrv0.axis1.encoder.pos_abs])
start_liveplotter(lambda: [odrv0.axis1.encoder.count_in_cpr])

odrv0.save_configuration()
odrv0.reboot()

https://docs.odriverobotics.com/v/0.5.6/control.html#control-doc

https://docs.odriverobotics.com/v/0.5.5/fibre_types/com_odriverobotics_ODrive.html#ODrive.Encoder.Mode
https://discourse.odriverobotics.com/t/two-absolute-encoders-to-odrive/5303/2

https://discourse.odriverobotics.com/t/issues-with-amt232b-v-encoder/5944

dump_errors(odrv0)
odrv0.clear_errors()

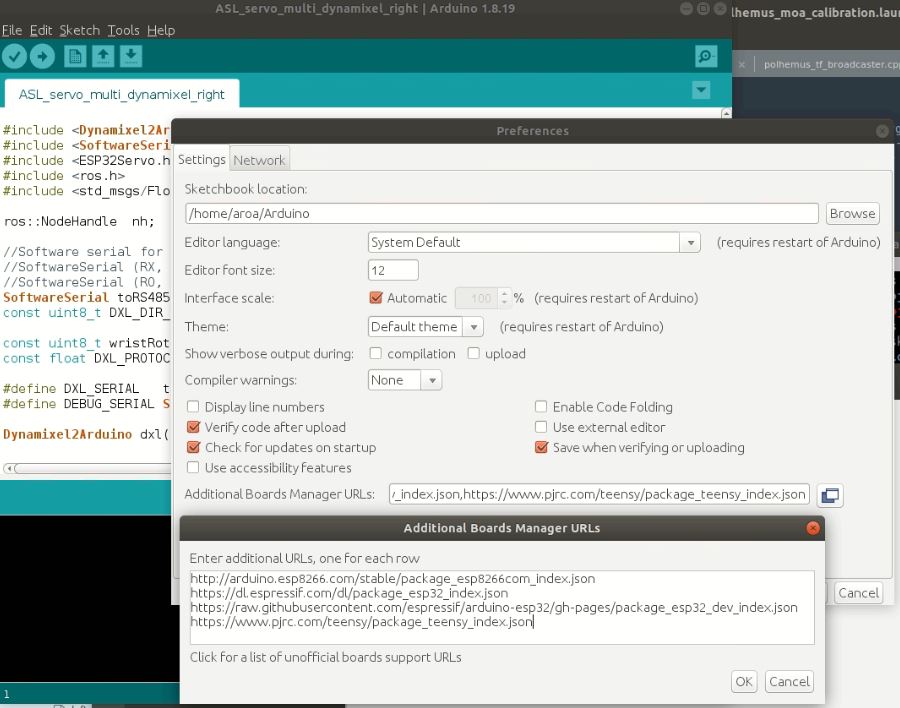
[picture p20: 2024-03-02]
images/readme/arduino-esp32.jpg

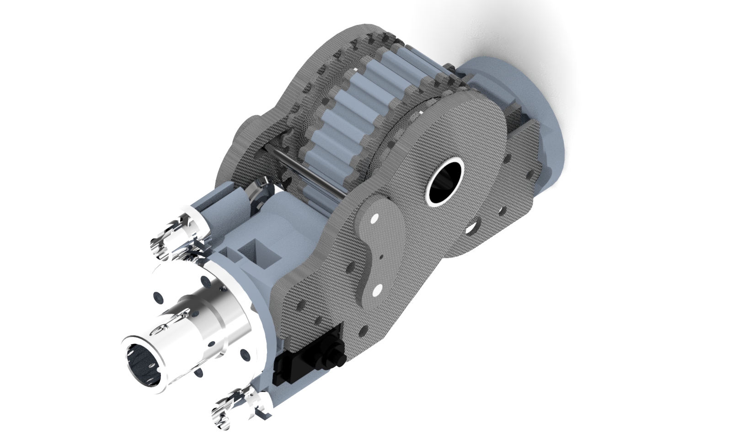
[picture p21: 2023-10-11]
images/readme/obmp-elb-1300.jpg

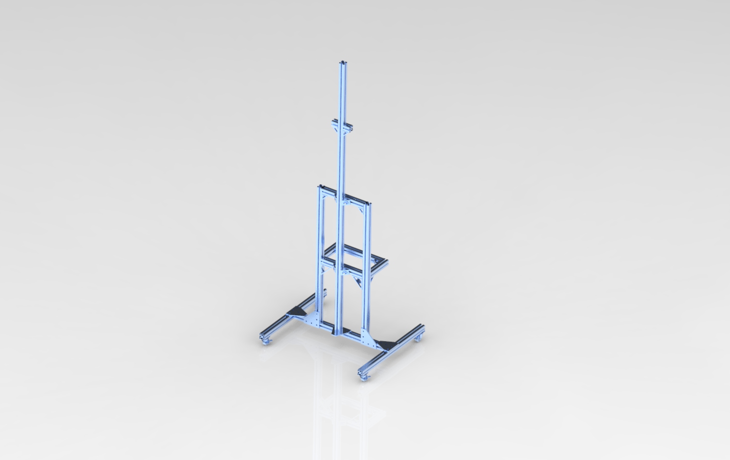
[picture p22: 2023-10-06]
images/readme/OBMP-BA-H-1000.jpg

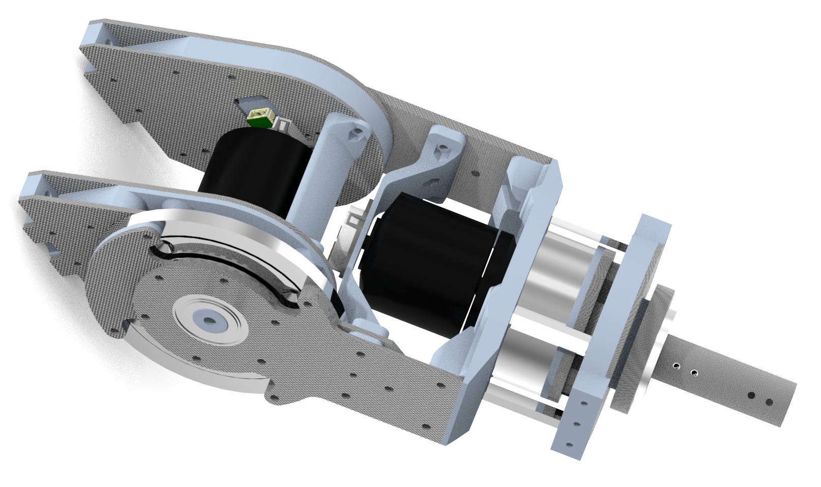
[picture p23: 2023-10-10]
images/readme/obmp-sar-1200.jpg

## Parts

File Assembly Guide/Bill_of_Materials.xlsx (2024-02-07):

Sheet: Bimanual_Robot_Arm_TypeA
Item | Product Number/SKU | Units | Unit Price/ USD | Subtotal/USD | Website | Notes
ODrive v3.6 - 56V with Connectors | ODRIVE V3.6 (NRND) | 6 | 259 | 1554 | https://odriverobotics.com/shop/odrive-v36 | NRND - Alternative is Odrive S1 or Pro. Or Other VESCs
Dual Shaft Motor - D6374 150KV | D6374 150KV | 10 | 119 | 1190 | https://odriverobotics.com/shop/odrive-custom-motor-d6374-150kv
DYNAMIXEL XM540-W270-R | 902-0133-000 | 2 | 429.9 | 859.8 | https://www.robotis.us/dynamixel-xm540-w270-r/ | Forearm rotation actuator
harmonic gear reducer XB3-B | XB3-60-100 | 9 | 330 | 2970 | https://www.hanzh.com/harmonic-gear-reducer-XB3-B-p.html | Order 10 to replace the custom pulley system
AMT232B-V ROTARY ENCODR ABS 16384PPR/14BIT | 102-4485-ND | 10 | 49.63 | 496.3 | https://www.digikey.com/en/products/detail/cui-devices/AMT232B-V/8031587 | Can use AMT10E2-V or CUI AMT102-V instead for easier interfacing
5025790000 CONN 24-28AWG CRIMP TIN | WM9735CT-ND | 100 | 0.0273 | 2.73 | https://www.digikey.com/en/products/detail/molex/5025790000/2819012
5025780600 CONN PLUG HSG 6CKT BEIGE | WM15814-ND | 20 | 0.39 | 7.8 | https://www.digikey.com/en/products/detail/molex/5025780600/2819002
IC BUF NON-INVERT 5.5V SOT353 | 74AHC1G125SE-7DICT-ND | 10 | 0.245 | 2.45 | https://www.digikey.com/en/products/detail/diodes-incorporated/74AHC1G125SE-7/2639244 | buffer chip required for AMT232B-V due to manufacture error | https://discourse.odriverobotics.com/t/issues-with-amt232b-v-encoder/5944
Raspberry Pi 4 Model B 4GB Dual Monitors Starter Kit | 2005283 | 1 | 119.95 | 119.95 | https://www.okdo.com/us/p/okdo-raspberry-pi-4-4gb-essential-starter-kit-us-version/ | ROS Ethernet to SPI interface for CANBUS. Alternatively can use other SBC or computation modules
Carbon Fiber Round Tube 500x25x23mm - opt: 25x23 Plain Glossy |  | 1 | 24 | 24 | https://www.aliexpress.com/item/32870874499.html | Structural materials
Carbon Fiber Sheet 200 x 250 x 5mm - opt: 5.0mm Twill Glossy |  | 15 | 65 | 975 | https://www.aliexpress.com/item/32963597194.html | Materials for waterjet cutting
Carbon Fiber Sheet 200 x 250 x 3mm - opt: 3.0mm Twill Glossy |  | 20 | 32.99 | 659.8 | https://www.aliexpress.com/item/32692185829.html | Materials for waterjet cutting
Carbon Fiber Sheet 200 x 250 x 2mm - opt: 2.0mm Twill Glossy |  | 5 | 24.99 | 124.95 | https://www.aliexpress.com/item/32692185829.html | Materials for waterjet cutting
Goteck Micro Metal Gear Servo (2.5kg) | SER0011 | 4 | 7.8 | 31.2 | https://www.dfrobot.com/product-121.html | Locking servos for elbow
FEETECH High-Torque Servo FS5115M | 3426 | 4 | 19.95 | 79.8 | https://www.pololu.com/product/3426 | locking servos for shoulder
Dyneema 2mm Superound 78 - Black | RASK7802 | 10 | 1.44 | 14.4 | https://chainsropesandanchors.co.nz/Rope-Cordage/Dyneema-Braid-Uncovered/2mm-dyneema-braid | High strength cables for tendons and Bowden transmission
Dyneema 3mm Dyneforce 99 - White | RASK99003 | 5 | 2.6 | 13 | https://chainsropesandanchors.co.nz/Dyneema-3mm-SK99-HS | High strength cables for tendons and Bowden transmission
Thimbles 3mm Wedled 316 Stainless | RF2181 | 8 | 3.77 | 30.16 | https://chainsropesandanchors.co.nz/Thimbles/Ronstan-3mm-stainless-lashing-thimble | Connector terminal for cables
Bowden Sleeve - WHITES CABLE BOWDEN OUTER 7mm X 25ft NYLON LINED | HWCO7NL | 1 | 37.7 | 37.7 | https://motozone.co.nz/collections/bowden-cable-parts/products/hwco7nl | Bowden set
Bowden Endcaps - MOTION PRO CABLE END CAP FOR 7mm OUTER PKT of 10 (D) | MP010006 | 1 | 8.2 | 8.2 | https://motozone.co.nz/collections/bowden-cable-parts/products/mp010006 | Bowden set
Bowden adjuster set - WHITES CABLE ADJUSTER WITH NUT- 9mm ID FIT | HWCADJ9 | 8 | 3.93 | 31.44 | https://motozone.co.nz/collections/bowden-cable-parts/products/hwcadj9 | Bowden set
Female Threaded Hex Standoff, 18-8 Stainless Steel, 10mm Hex, 51mm Long, M5 x 0.8mm Thread | 94868A768 | 12 | 5.39 | 64.68 | https://www.mcmaster.com/94868A768/ | Structural support for torso
Machine Key, 316 Stainless Steel, 6 mm x 6 mm, 20 mm Long, Undersized | 98870A339 | 2 | 11.17 | 22.34 | https://www.mcmaster.com/98870A339/ | Custom machine key for XB3 Harmonic drives
Needle-Roller Bearing, Open, for 5 mm Shaft Diameter | 5905K349 | 4 | 6.39 | 25.56 | https://www.mcmaster.com/5905K349/ | Also known as HK0508
316 Stainless Steel Dowel Pin, 6 mm Diameter, 32 mm Long, Pkt of 5 | 93600A655 | 2 | 10.71 | 21.42 | https://www.mcmaster.com/93600A655/ | Locking mechanism latch pins
Rotary Shaft, 316 Stainless Steel, 4 mm Diameter, 200 mm Long | 1265K37 | 1 | 19.11 | 19.11 | https://www.mcmaster.com/1265K37/ | Misc. pins
Rotary Shaft, 316 Stainless Steel, 5 mm Diameter, 200 mm Long | 1265K44 | 1 | 23.9 | 23.9 | https://www.mcmaster.com/1265K44/ | Misc. pins
RS PRO 51110 Thrust Ball Bearing- Open Type End Type, 50mm I.D, 70mm O.D | 205-8826 | 4 | 9.97 | 39.88 | https://nz.rs-online.com/web/p/ball-bearings/2058826 | Arm rotation connection. Note : SKF51110
RS PRO Silver Stainless Steel Round Tube, 300mm Length, Dia. 20mm | 786-6181 | 3 | 26.32 | 78.96 | https://nz.rs-online.com/web/p/tubing-and-profile-struts/7866181 | Elbow connector pin
RS PRO Zinc Plated Mild Steel Threaded Rod, M8, 200mm, Pkt of 5 | 175-7027 | 2 | 5.39 | 10.78 | https://nz.rs-online.com/web/p/threaded-rods/1757027 | Torso box structural connector
Lazy Susan Bearing Turntable Ring, 140mm/5.5in - 8mm/0.31in thick | ASL140-085 | 4 | 31.68 | 126.72 | https://www.amazon.com/Bearing-Turntable-11-8in-13-8in-15-4in/dp/B08JYKMY21 | Low cost loading bearing | https://www.timberlywoodturning.co.nz/products.php?product=Lazy-Susan-Aluminium-140-mm-D-x-8.5mm
6806ZZ Deep Groove Ball Bearings 30mm Inner Dia 42mm OD 7mm Bore Double Shielded Chrome Steel Z2 10pcs | 6806ZZ | 13 | 1.499 | 19.487 | https://www.amazon.com/uxcell-6806ZZ-Groove-Bearings-Shielded/dp/B082PY8F6G/ | Misc bearings
608ZZ Deep Groove Ball Bearing Double Shield 8mm x 22mm x 7mm High Carbon Steel Z1 Bearings 4pcs | 608ZZ | 3 | 1.6225 | 4.8675 | https://www.amazon.com/uxcell-Groove-Bearing-Double-Bearings/dp/B07FDYTJS5/ | Misc bearings
6804ZZ Deep Groove Ball Bearings 20mm Bore 32mm OD 7mm Thickness Double Shielded Chrome Steel Z2 10pcs | 6804ZZ | 18 | 1.249 | 22.482 | https://www.amazon.com/uxcell-6804ZZ-Groove-Bearings-Shielded/dp/B082PWB7R5 | Misc bearings
16004ZZ 16005ZZ 16006ZZ Thin Wall Bearing Deep Groove Ball Bearings Metal Shielded Bearing Bearing Steel 1Pcs (Size : 1PCS, Color : 16004ZZ(20x42x8mm)) | 16004ZZ | 7 | 24.02 | 168.14 | https://www.amazon.com/16004ZZ-16005ZZ-16006ZZ-Bearings-Shielded/dp/B0CGHPKZKT | Misc bearings
Openbuilds Stainless Steel V-Slot Wheel - 625zz Bearing Pulley Metal Double V Gear Aluminum Extrusion 3D Printer Parts [13pcs of Pack] |  | 1 | 25.99 | 25.99 | https://www.amazon.com/Openbuilds-Stainless-Bearing-Aluminum-Extrusion/dp/B09PDGJSH7/ | V522ZZ
Preamer Industrial Bearing Steel V Groved Wire Pulley Bearing Wheels Roller V Groove Sealed Guide Rail Ball Bearings 5x22x5mm, 5 Pcs | B015J4UU7Y | 2 | 14.21 | 28.42 | https://www.amazon.com/Bearing-Groved-Pulley-Wheels-Roller/dp/B015J4UU7Y/ | Misc bearings
Misc bolts and nuts |  | 1 |  |  |  | bolts and nuts of various size and length (WIP)
Machined parts
OBMP-MOTOR-COUPLER.stp | SS316 | 9 | 23.25 | 209.25 | https://www.pcbway.com/rapid-prototyping/manufacture/?type=1
OBMP-BTP-1632.stp | SS316 | 1 | 37.84 | 37.84 | https://www.pcbway.com/rapid-prototyping/manufacture/?type=1
OBMP-TUBE-COUPLER-25mm.stp | AL6061 | 5 | 29.98 | 149.9 | https://www.pcbway.com/rapid-prototyping/manufacture/?type=1
OBMP-BTP-1643 | AL6061 | 1 | 39.33 | 39.33 | https://www.pcbway.com/rapid-prototyping/manufacture/?type=1
 |  |  | Subtotal | 10371.7365
Printed PLA parts
obmp-tb-1010.stp |  | 2 | 33.27 | 66.54 | https://www.pcbway.com/rapid-prototyping/manufacture/?type=1
OBMP-TCU-1110 |  | 2 | 28.38 | 56.76
OBMP-TCU-1120 |  | 4 | 5.6 | 22.4
OBMP-TCU-1121 |  | 2 | 7.59 | 15.18
OBMP-TCU-1130 |  | 2 | 19.91 | 39.82
OBMP-TCU-1140 |  | 2 | 25.04 | 50.08
OBMP-TCU-1141 |  | 2 | 3.89 | 7.78
OBMP-TCU-1143 |  | 2 | 3.89 | 7.78
OBMP-TCU-1150 |  | 2 | 4.61 | 9.22
OBMP-TCU-1155 (Alternative sensor stand) |  | 2 | 7.1 | 14.2
OBMP-TCU-1160 |  | 2 | 47.62 | 95.24
OBMP-TCU-1161 |  | 2 | 5.48 | 10.96
OBMP-TCU-1170 |  | 2 | 39.82 | 79.64
OBMP-TCU-1180 |  | 2 | 14.31 | 28.62
OBMP-TCU-1183 |  | 2 | 3.98 | 7.96
OBMP-TCU-1185 (locking ring) |  | 4 | 3.49 | 13.96
OBMP-TCU-1186 (flexion arm mounting) |  | 2 | 21.16 | 42.32
OBMP-TCU-1189 (ratchet core) |  | 8 | 2.49 | 19.92
OBMP-SAR-1210 |  | 2 | 12.57 | 25.14
OBMP-SAR-1213 |  | 2 | 2.73 | 5.46
OBMP-SAR-1214 |  | 2 | 3.98 | 7.96
OBMP-SAR-1220 |  | 2 | 18.55 | 37.1
OBMP-SAR-1231 |  | 2 | 3.98 | 7.96
OBMP-SAR-1234 |  | 2 | 3.98 | 7.96
OBMP-SAR-1236 |  | 2 | 3.98 | 7.96
OBMP-SAR-1240 |  | 2 | 26.47 | 52.94
OBMP-SAR-1241 |  | 2 | 6.6 | 13.2
OBMP-SAR-1250 |  | 2 | 3.98 | 7.96
OBMP-SAR-1255 |  | 2 | 5.98 | 11.96
OBMP-SAR-1260 |  | 2 | 12.08 | 24.16
OBMP-SAR-1261 |  | 2 | 3.98 | 7.96
OBMP-FAM-A-1410 |  | 2 | 13.19 | 26.38
OBMP-FAM-A-1420 |  | 2 | 3.89 | 7.78
OBMP-FAM-A-1430 |  | 2 | 3.89 | 7.78
OBMP-FAM-A-1440 |  | 2 | 4.73 | 9.46
OBMP-ELB-1310 |  | 2 | 13.82 | 27.64
OBMP-ELB-1320 |  | 2 | 15.08 | 30.16
OBMP-ELB-1322 |  | 4 | 2.49 | 9.96
OBMP-ELB-1323 |  | 4 | 10.21 | 40.84 |  | Cheaper if cut from 50 mm alu tube
OBMP-TCU-1130 |  | 1 | 19.91 | 19.91
OBMP-BTU-1520 |  | 1 | 27.88 | 27.88
OBMP-BTU-1530 |  | 1 | 10.46 | 10.46
OBMP-BTU-1534 |  | 1 | 7.96 | 7.96
OBMP-BTP-1620 (base mount C) |  | 1 | 23.89 | 23.89
OBMP-BTP-1621 (base mount B) |  | 1 | 14.69 | 14.69
OBMP-BTP-1622 (base mount A) |  | 1 | 23.4 | 23.4
OBMP-BTP-1625 (bearing caps) |  | 6 | 2.49 | 14.94
OBMP-BTP-1630 (motor mount A) |  | 1 | 7.96 | 7.96
OBMP-BTP-1631 (motor mount B) |  | 1 | 7.96 | 7.96
OBMP-BTP-1640 (output mount) |  | 2 | 11.45 | 22.9
OBMP-BTP-1642 (output puck core) |  | 1 | 7.96 | 7.96
OBMP-BTP-1653 (idler wheel) |  | 12 | 6.16 | 73.92
 |  |  | Subtotal | 1229.93
A pair of OpenBMP arms (excluding forearm modules) |  |  | Total | 11601.6665

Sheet: Stand
Items | product number/SKU | Units | Unit Price/ USD | Subtotal/USD | Website | Notes | Price per cm
4040 Aluminium Extrusion - 720 mm | 5537T904 | 1 | 62.64 | 62.64 | https://www.mcmaster.com/5537T904/ | T-Slotted Framing, Single 4-Slot Rail, Silver, 40 mm Square, Solid | 0.87
4040 Aluminium Extrusion - 700 mm | 5537T904 | 2 | 60.9 | 121.8 | https://www.mcmaster.com/5537T904/
4040 Aluminium Extrusion - 1000 mm | 5537T904 | 2 | 87 | 174 | https://www.mcmaster.com/5537T904/
4040 Aluminium Extrusion - 320 mm | 5537T904 | 3 | 27.84 | 83.52 | https://www.mcmaster.com/5537T904/
4040 Aluminium Extrusion - 2000 mm | 5537T904 | 1 | 174 | 174 | https://www.mcmaster.com/5537T904/
4040 Aluminium Extrusion - 50 mm | 5537T904 | 2 | 4.35 | 8.7 | https://www.mcmaster.com/5537T904/
4040 Aluminium Extrusion - 200 mm | 5537T904 | 2 | 17.4 | 34.8 | https://www.mcmaster.com/5537T904/
T-Slotted Framing, Silver Tee Surface Bracket for 40mm High Single Rail | 5537T973 | 3 | 19.29 | 57.87 | https://www.mcmaster.com/5537T973/ | OBMP-BA-H-FAST-T
T-Slotted Framing, Silver 90 Degree Surface Bracket for 40mm Single Rail | 5537T964 | 2 | 17.57 | 35.14 | https://www.mcmaster.com/5537T964/ | OBMP-BA-H-FAST-L
T-Slotted Framing, Gusset Bracket for 40 mm High Rail, 3-1/8" Long, Silver | 5537T66 | 2 | 13.14 | 26.28 | https://www.mcmaster.com/5537T66/ | OBMP-BA-H-FAST-G1
T-Slotted Framing, Gusset Bracket for 40mm High Rail, 1-37/64" Long | 5537T586 | 12 | 8.48 | 101.76 | https://www.mcmaster.com/5537T586/ | OBMP-BA-H-FAST-G2 | https://www.mcmaster.com/6812N831/
Cart-Smart Caster, Swivel with Brake and 2" Diameter Gray Rubber Wheel | 78155T32 | 4 | 7.25 | 29 | https://www.mcmaster.com/78155T32/ | https://nz.rs-online.com/web/p/castor-wheels/1253752 | https://www.mcmaster.com/2834T23/ | https://www.mcmaster.com/78155T62/
Misc bolts and nuts
 |  |  | Subtotal | 909.51

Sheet: One_Unit_of_Forearm_ASL_Hand
Items | product number/SKU | Units | Unit Price/ USD | Subtotal/USD | Website | Notes
FEETECH High-Torque Servo FS5115M | 3426 | 2 | 19.95 | 39.9 | https://www.pololu.com/product/3426
Goteck Micro Metal Gear Servo (2.5kg) | SER0011 | 12 | 7.8 | 93.6 | https://www.dfrobot.com/product-121.html
Dyneema 1mm SK75 Dyneema Braid 40mtr Mini reel | RADMR1 | 1 | 17 | 17 | https://chainsropesandanchors.co.nz/Rope-Cordage/0-to-4mm/Dyneema-Braid-Armare-1mm
AC/DC Power Supply, Medical, 1 Output, 40 W, 6 V, 6.66 A | 3320600000 | 1 | 68.48 | 68.48 | https://www.newark.com/mascot/3320600000/adapter-ac-dc-6v-6-66a-rohs-compliant/dp/54AJ3118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
ESP32 Development Board - 38 Pin - ESPWROOM- 32D |  | 1 | 9.99 | 9.99 | https://www.amazon.com/HiLetgo-ESP-WROOM-32-Development-Microcontroller-Integrated/dp/B0718T232Z
Misc bolts and nuts
OBMP-FAH-1810 |  | 1 | 7.96 | 7.96 | https://www.pcbway.com/rapid-prototyping/manufacture/?type=1
OBMP-FAH-1811 (Optional) |  | 1 | 7.96 | 7.96
OBMP-FAH-1820 |  | 1 | 23.15 | 23.15
OBMP-FAH-1830 |  | 1 | 7.96 | 7.96
OBMP-FAH-1840 |  | 2 | 3.98 | 7.96
OBMP-FAH-1841 |  | 2 | 3.98 | 7.96
OBMP-FAH-1842 |  | 10 | 2.49 | 24.9
OBMP-FAH-1851 |  | 1 | 7.96 | 7.96
OBMP-FAH-1856 |  | 1 | 7.96 | 7.96
OBMP-FAH-1857 |  | 1 | 7.96 | 7.96
OBMP-FAH-1858 |  | 4 | 2.49 | 9.96
OBMP-FAH-1852 |  | 1 | N/A
OBMP-FAH-1853 |  | 1 | N/A
OBMP-FAH-1854 |  | 1 | N/A
OBMP-FAH-1855 |  | 1 | N/A
NINJAFLEX 3D PRINTER FILAMENT (85A) | 3DNF0017510 | 1 | 90.61 | 90.61 | https://ninjatek.com/shop/ninjaflex/ | Material spool for flexible fingers
 |  |  | Subtotal | 441.27

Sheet: One_Unit_of_Dynamixel_Hand
Items | product number/SKU | Units | Unit Price/ USD | Subtotal/USD | Website | Notes
DYNAMIXEL XM430-W350-T | 902-0124-000 | 2 | 269.9 | 539.8 | https://www.robotis.us/dynamixel-xm430-w350-t/
DYNAMIXEL XC330-T288-T | 902-0171-000 | 12 | 89.9 | 1078.8 | https://www.robotis.us/dynamixel-xc330-t288-t/
Dyneema 1mm SK75 Dyneema Braid 40mtr Mini reel | RADMR1 | 1 | 17 | 17 | https://chainsropesandanchors.co.nz/Rope-Cordage/0-to-4mm/Dyneema-Braid-Armare-1mm
MR52ZZ |  | 24 | 1.099 | 26.376 | https://www.amazon.com/Bearing-2x5x2-5-Miniature-Bearings-Quality/dp/B081SVP2DF
MF52ZZ |  | 12 | 1.298 | 15.576 | https://www.amazon.com/uxcell-Miniature-Flange-Bearings-Shielded/dp/B07SLZGZW5
Misc bolts and nuts
OBMP-FDH-1740 | 1265K17 | 2 | 15.27 | 30.54 | https://www.mcmaster.com/1265K17/
OBMP-FDH-1710 |  | 1 | 29.13 | 29.13 | https://www.pcbway.com/rapid-prototyping/manufacture/?type=1
OBMP-FDH-1720 |  | 2 | 9.34 | 18.68
OBMP-FDH-1730 |  | 1 | 7.96 | 7.96
OBMP-FDH-1751 |  | 1 | 7.96 | 7.96
OBMP-FDH-1752 |  | 1 | 7.96 | 7.96
OBMP-FDH-1754 |  | 1 | 7.96 | 7.96
OBMP-FDH-1758 |  | 4 | 2.49 | 9.96
OBMP-FDH-1760 |  | 12 | 2.49 | 29.88
OBMP-FDH-1753 |  | 1 | N/A
OBMP-FDH-1755 |  | 1 | N/A
OBMP-FDH-1756 |  | 1 | N/A
OBMP-FDH-1757 |  | 1 | N/A
NINJAFLEX 3D PRINTER FILAMENT (85A) | 3DNF0017510 | 1 | 90.61 | 90.61 | https://ninjatek.com/shop/ninjaflex/
 |  |  | Subtotal | 1918.192

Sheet: One_Unit_of_Robotic_Wrist
Items | product number/SKU | Units | Unit Price/ USD | Subtotal/USD | Website | Notes
6805ZZ |  | 2 | 3.245 | 6.49 | https://www.amazon.com/uxcell-Bearing-25x37x7mm-Shielded-Bearings/dp/B07TJFL7N8
F6805ZZ |  | 1 | 6.49 | 6.49 | https://www.amazon.com/uxcell-F6805ZZ-Shielded-Bearings-25x37x7mm/dp/B07XYM9DCC/
Misc bolts and nuts
DYNAMIXEL XM540-W270-R | 902-0133-000 | 2 | 429.9 | 859.8 | https://www.robotis.us/dynamixel-xm540-w270-r/
DYNAMIXEL XM430-W350-T | 902-0124-000 | 1 | 269.9 | 269.9 | https://www.robotis.us/dynamixel-xm430-w350-t/
FlexLink Silver Aluminium Profile Strut, 22 x 22 mm, 5.6mm Groove, 1000mm Length, Series XD |  | 1 | 11.98 | 11.98 | https://nz.rs-online.com/web/p/tubing-and-profile-struts/2490095 | OBMP-FWM-1680
OBMP-FWM-1610 |  | 1 | 19.42 | 19.42 | https://www.pcbway.com/rapid-prototyping/manufacture/?type=1
OBMP-FWM-1620 |  | 1 | 7.96 | 7.96
OBMP-FWM-1630 |  | 1 | 11.7 | 11.7
OBMP-FWM-1640 |  | 1 | 7.96 | 7.96
OBMP-FWM-1650 |  | 1 | 9.46 | 9.46
OBMP-FWM-1660 |  | 1 | 7.96 | 7.96
OBMP-FWM-1670 |  | 1 | 7.96 | 7.96
 |  |  | Subtotal | 1227.08

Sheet: Alternative_actuators
Items | product number/SKU | Units | Unit Price/ USD | Subtotal/USD | Website | Notes
9g 300° Clutch Servo | SER0053 |  | 5 |  | https://www.dfrobot.com/product-2118.html
6Kg 300° Clutch Servo | SER0057 |  | 9 |  | https://www.dfrobot.com/product-2121.html
HV Robot servo 60kg RDS5160 Metal Gear Digital servo arduino servo Large servo | RDS5160/270 | 1 | 53.99 | 53.99 | https://www.amazon.com/ZOSKAY-Robot-RDS5160-Digital-arduino/dp/B07S96K29Z | Alternative forearm rotation (TypeB)

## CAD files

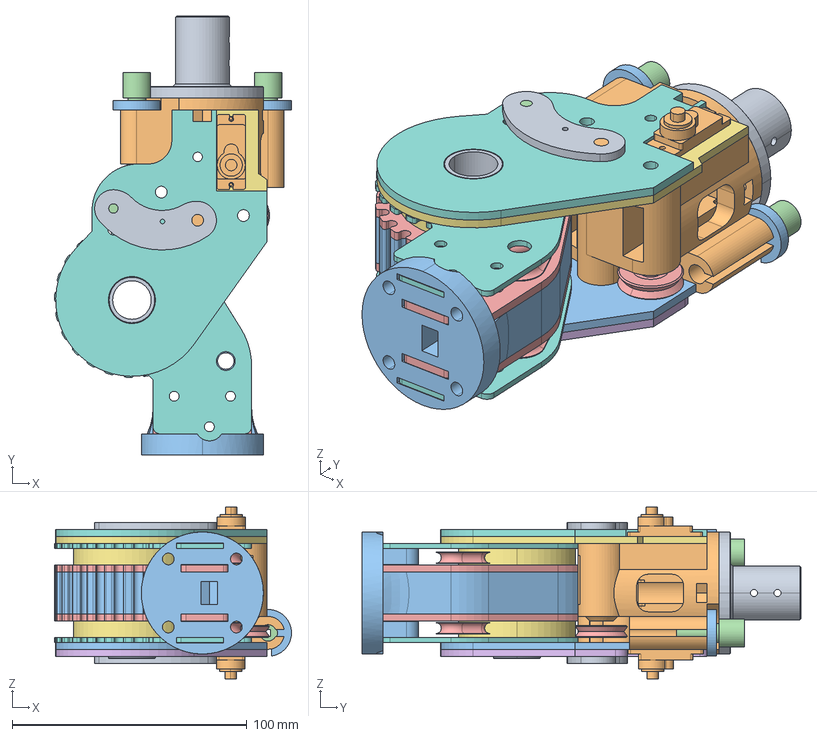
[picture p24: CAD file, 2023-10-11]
CAD/Elbow/obmp-elb-1300_asm.stp
101.0 x 187.0 x 73.2 mm
OBMP-TUBE-COUPLER-25MM
OBMP-ELB-1310
OBMP-ELB-P3-1311
HWCADJ9-CABLE-ADJUSTER x 2
V522ZZ-5MM-VGROOVE-BEARING x 2
OBMP-ELB-P3-1312
OBMP-ELB-P3-1313
OBMP-ELB-P3-1314
OBMP-ELB-P3-1315 x 2
OBMP-ELB-1316
OBMP-ELB-1320
OBMP-ELB-1317
OBMP-ELB-P3-1321 x 2
OBMP-ELB-1322 x 2
OBMP-ELB-1323 x 2
OBMP-ELB-P2-1324 x 2
OBMP-ELB-1330
GS-9025MG x 2
HWCADJ9-CABLE-ADJUSTER-NUT x 2
5905K349_HK0508_NEEDLE-ROLLER_B x 2
RF2181-RONSTAN-THIMBLE-4MM x 2

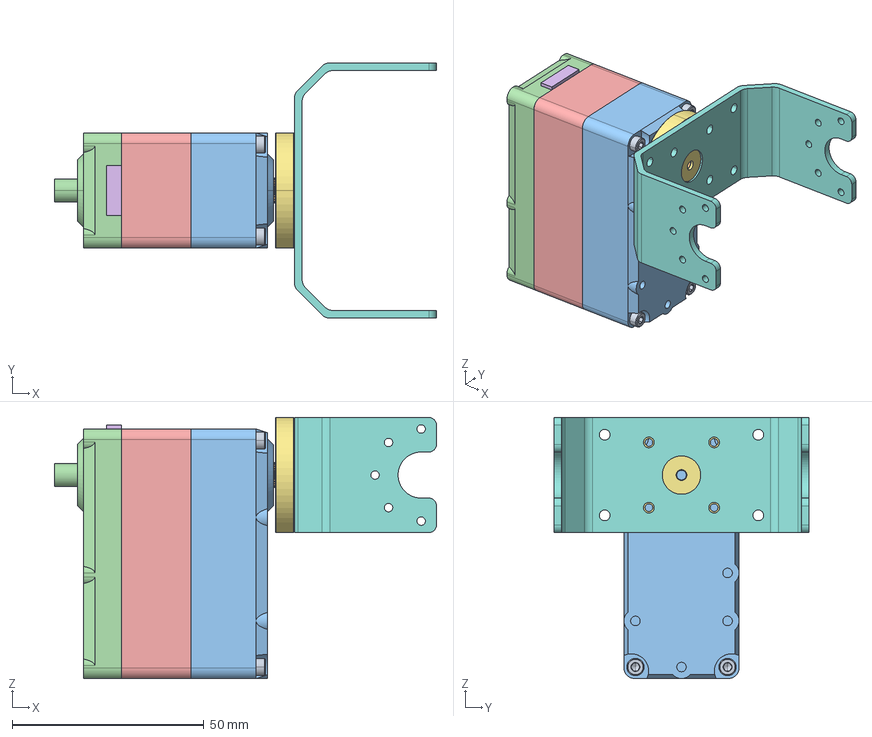
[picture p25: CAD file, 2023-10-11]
CAD/Forearm_Adaptor_Modules/rds5160_v39_asm.stp
99.5 x 66.5 x 68.0 mm
DIN_EN_ISO_4762_M2_5X25_IPT x 4
RDS3235_GEAR_25R_0_00
WHEEL_ASM
WHEEL_GEAR
SUPPORT_LARGE_2

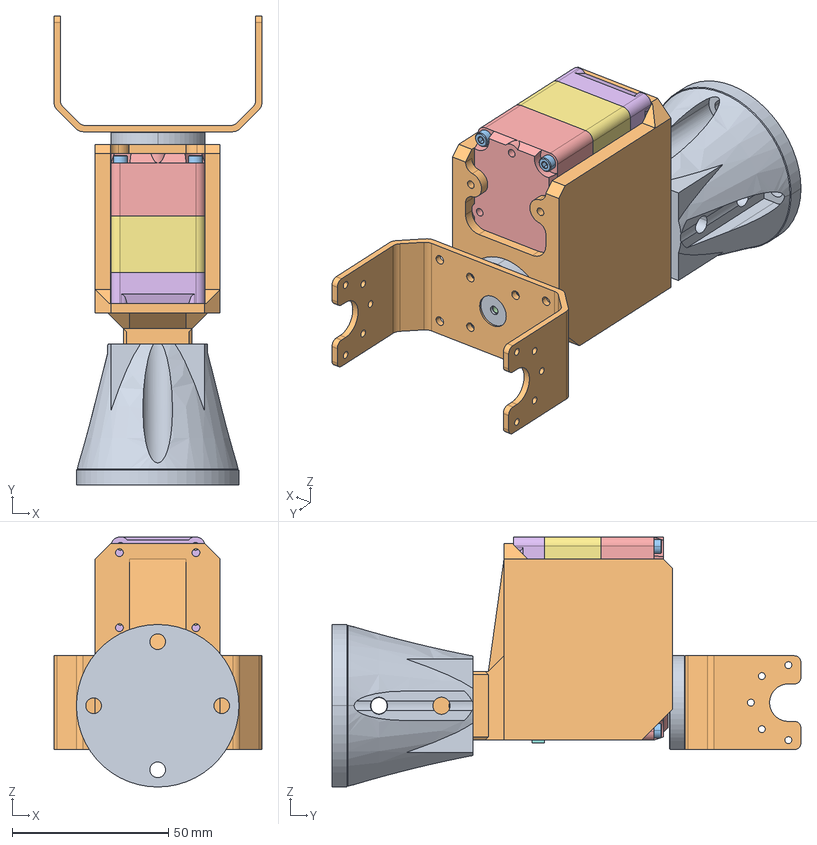
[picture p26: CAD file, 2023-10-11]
CAD/Forearm_Adaptor_Modules/obmp-fam-b-1400_asm.stp
66.5 x 150.0 x 80.0 mm
OBMP-FAM-B-1410
OBMP-FAM-B-1420
DIN_EN_ISO_4762_M2_5X25_IPT_1 x 4
RDS3235_GEAR_25R_0_00_1
WHEEL_ASM_1
WHEEL_GEAR_1
SUPPORT_LARGE_2_1

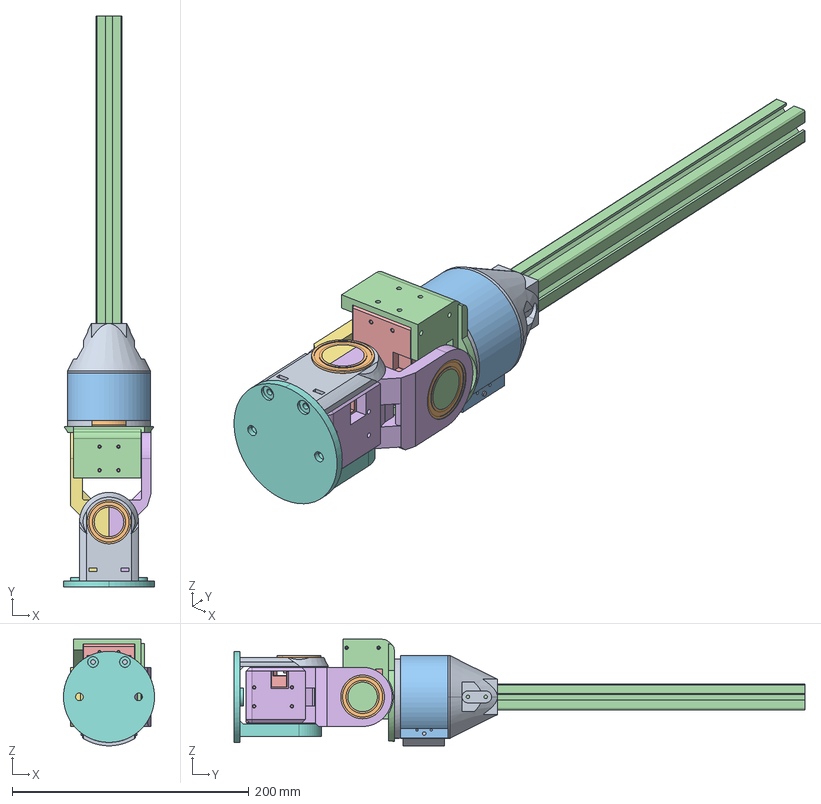
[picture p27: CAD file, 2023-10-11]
CAD/Forearm_Wrist_Module/obmp-fwm-1600_asm.stp
77.0 x 482.8 x 90.1 mm
OBMP-FWM-1610
F6806ZZ_30X42X7
OBMP-FWM-1620
OBMP-FWM-1630
XM_H-540_IDLE x 2
OBMP-FWM-1640
OBMP-FWM-1650
OBMP-FWM-1660
OBMP-FWM-1670
6805-ZZ x 2
XM_H-430_IDLER
OBMP-FWM-1680

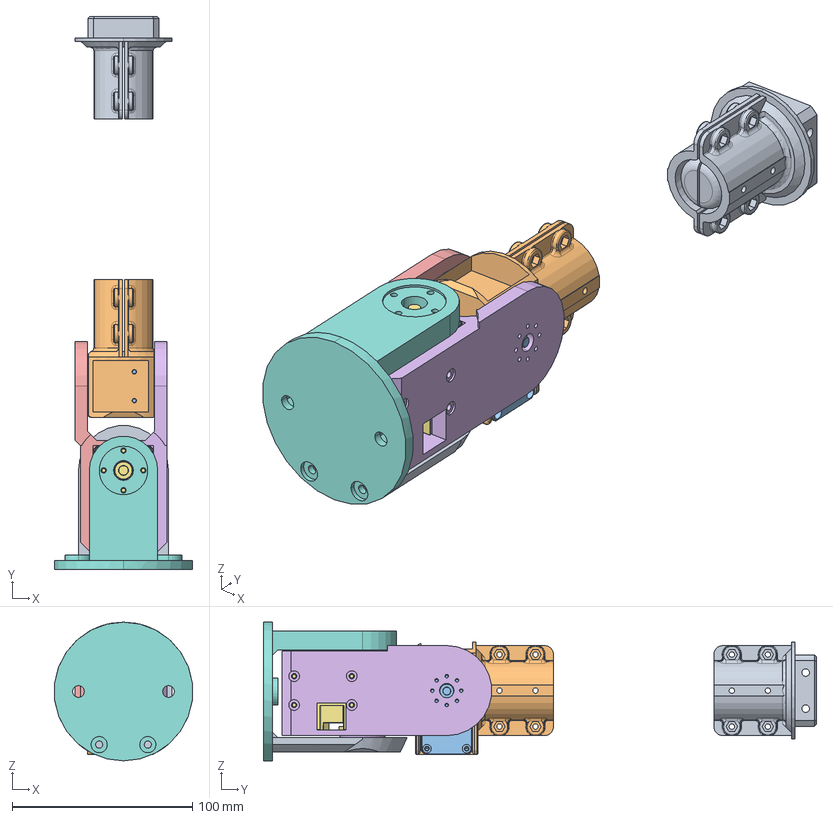
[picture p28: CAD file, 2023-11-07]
CAD/Forearm_Wrist_module_TypeA/obmp-fwm-a-1600_asm.stp
76.6 x 307.0 x 77.0 mm
OBMP-FMW-A-1610
OBMP-FWM-A-1620
XM_H-430_IDLER
6805-ZZ x 2
OBMP-FWM-A-1630
OBMP-FWM-A-1640
XM_H-540_IDLE
OBMP-FWM-A-1660
OBMP-FWM-A-1670

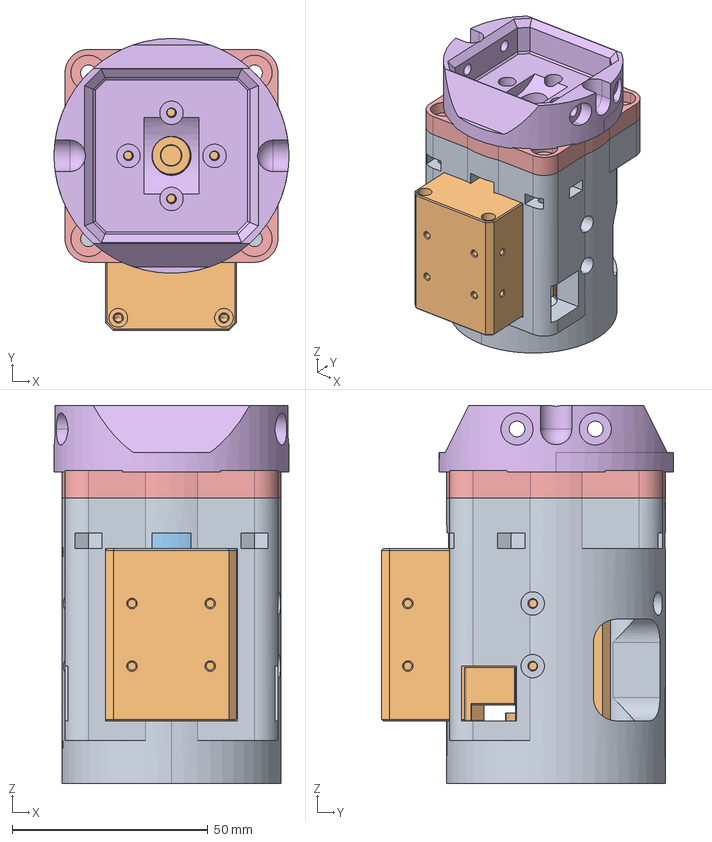
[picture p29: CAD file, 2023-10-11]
CAD/Forearm_Adaptor_Modules/obmp-fam-a-1400_asm.stp
60.0 x 74.7 x 96.6 mm
OBMP-FAM-A-1410
XM-540_IDLE
OBMP-FAM-A-1420
6806-ZZ-30X42X7_BEARING
OBMP-FAM-A-1430
OBMP-FAM-A-1440

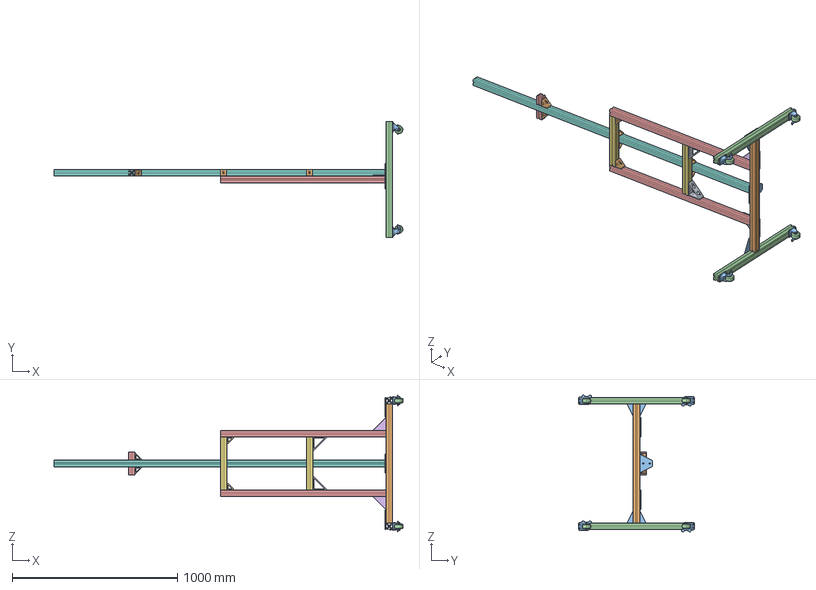
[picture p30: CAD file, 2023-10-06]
CAD/Base_Stand/obmp-ba-h-1000_asm.stp
2109.5 x 700.0 x 827.4 mm
OBMP-BA-H-1010
OBMP-BA-H-FAST-T x 3
OBMP-BA-H-1020 x 2
OBMP-BA-H-1030 x 2
OBMP-BA-H-FAST-L x 2
OBMP-BA-H-1040 x 2
OBMP-BA-H-1050
OBMP-BA-H-FAST-G1 x 2
OBMP-BA-H-FAST-G2 x 8
OBMP-BA-H-1100 x 4
OBMP-BA-H-1060 x 2

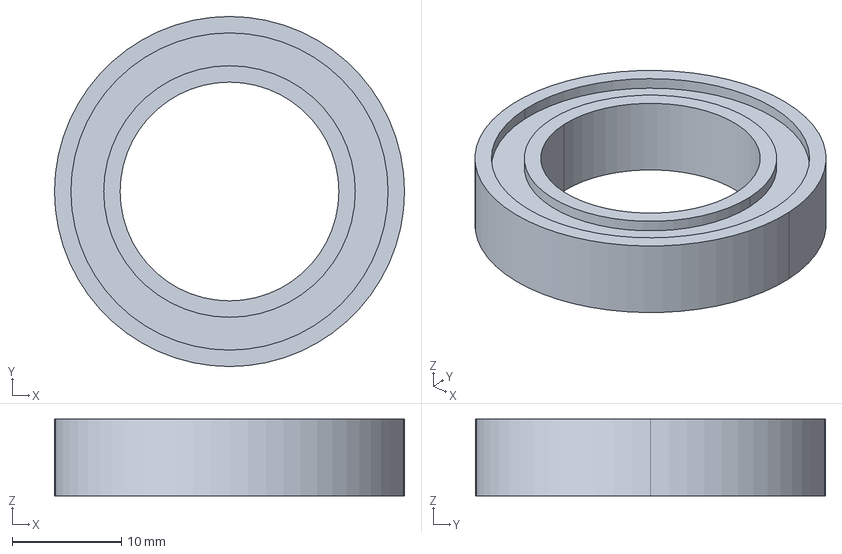
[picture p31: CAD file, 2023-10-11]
CAD/Back_Transmission_Pulley/6804_zz_bearing_20x32x7.stp
32.0 x 32.0 x 7.00 mm

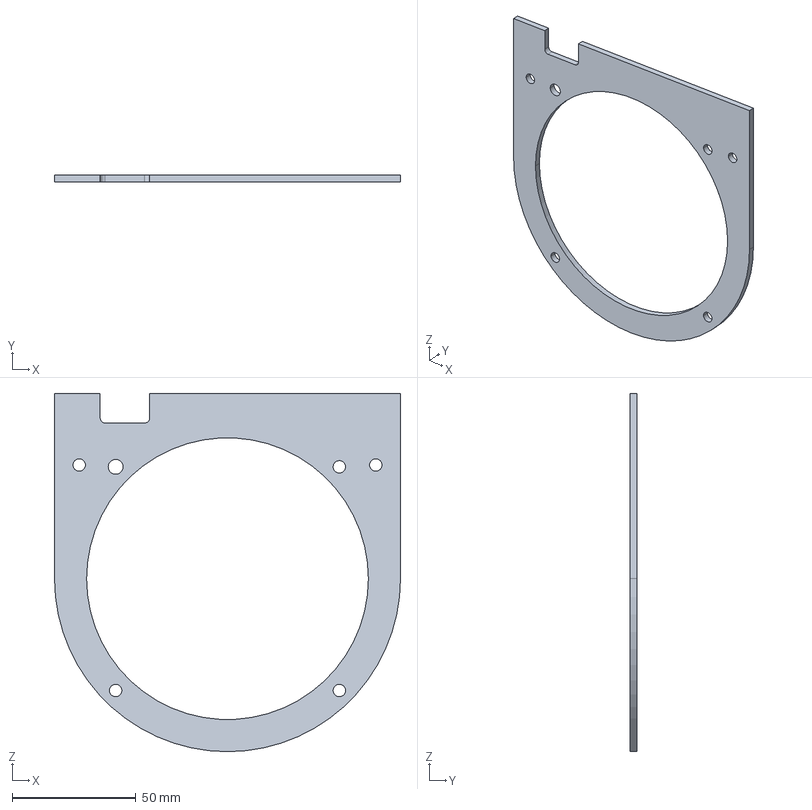
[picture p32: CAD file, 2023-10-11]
CAD/Back_Transmission_Unit/obmp-btu-p3-1532.stp
140.0 x 3.00 x 145.0 mm

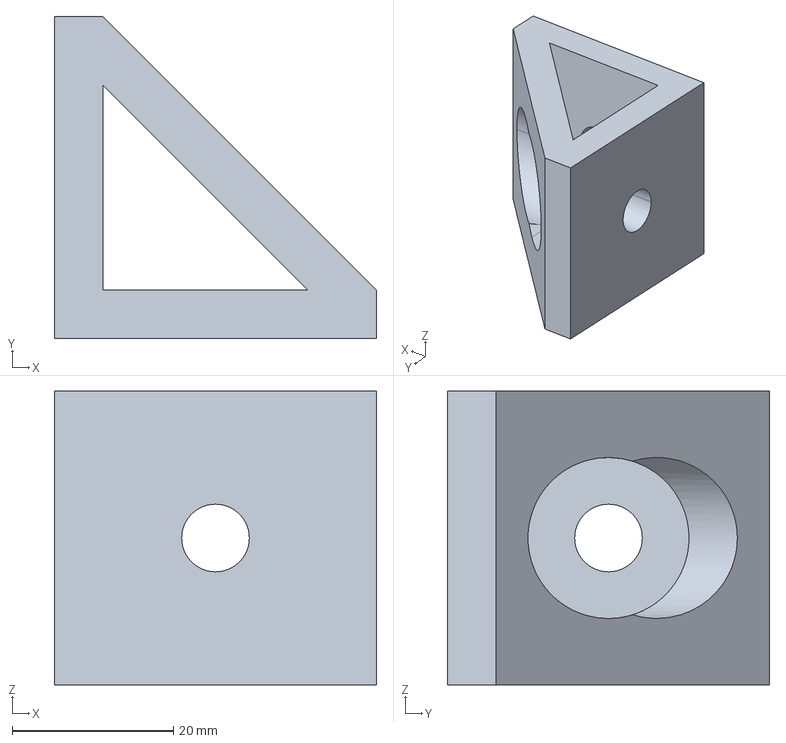
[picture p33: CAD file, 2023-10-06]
CAD/Base_Stand/obmp-ba-h-fast-g2.stp
40.0 x 40.0 x 36.5 mm

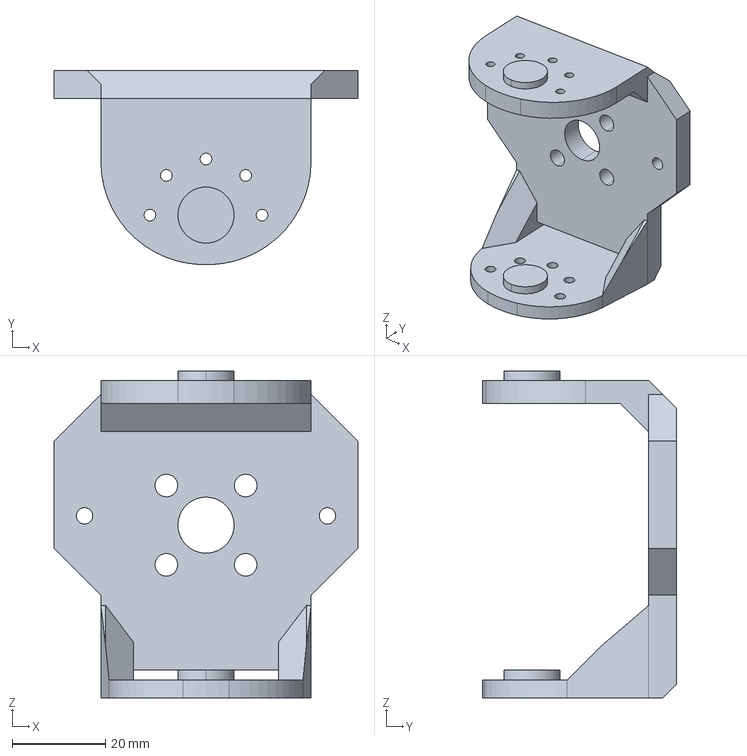
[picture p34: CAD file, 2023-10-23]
CAD/Forearm_ASL_Hand/obmp-fah-1811.stp
65.0 x 41.6 x 70.0 mm

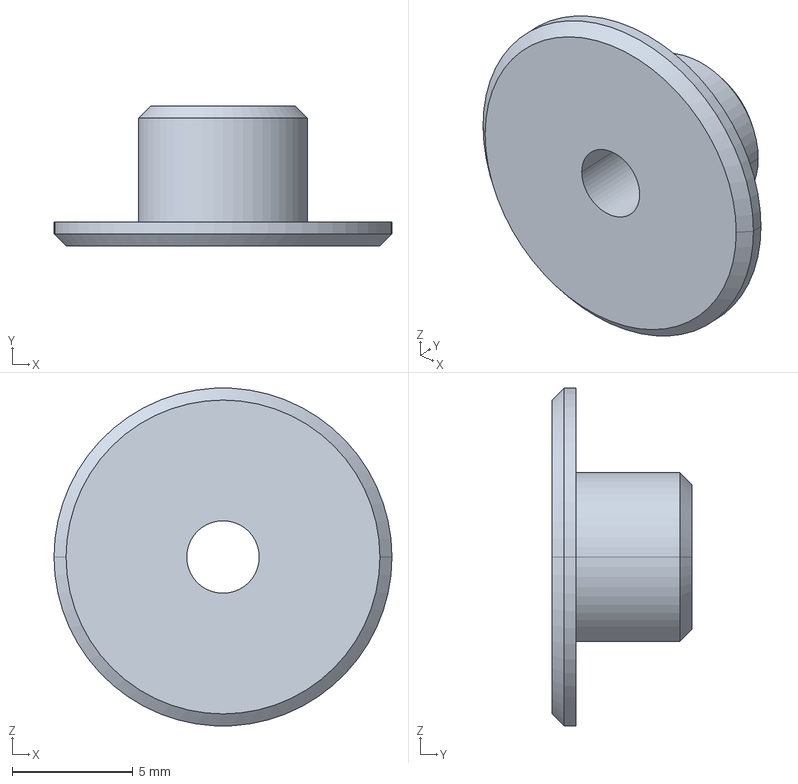
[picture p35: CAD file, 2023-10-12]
CAD/Forearm_Dynamixel_Hand/obmp-fdh-1758.stp
14.0 x 5.80 x 14.0 mm

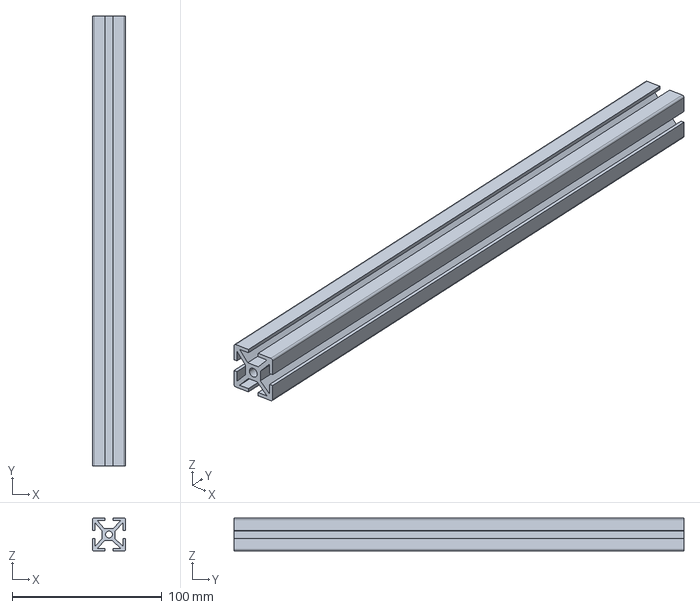
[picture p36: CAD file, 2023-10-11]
CAD/Forearm_Wrist_Module/obmp-fwm-1680.stp
22.0 x 300.0 x 22.0 mm

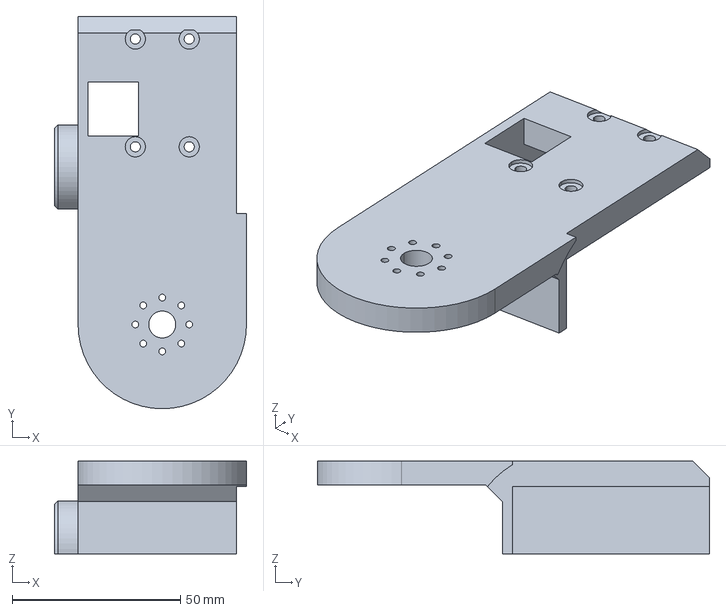
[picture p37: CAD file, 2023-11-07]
CAD/Forearm_Wrist_module_TypeA/obmp-fwm-a-1640.stp
57.0 x 116.5 x 27.5 mm

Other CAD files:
CAD/Misc/esp_board_a.stp
CAD/Shoulder_Abd_Rot/obmp-sar-1241.stp
CAD/Torso_Box/obmp-tb-p-1020.stp
CAD/Torso_Clavicle_Unit/OBMP-TCU-1170-S.stp
CAD/Back_Transmission_Pulley/16004-zz-20x42x8_bearing.stp
CAD/Back_Transmission_Pulley/D6374-150KV.step
CAD/Back_Transmission_Pulley/hwcadj9-cable-adjuster-nut.stp
CAD/Back_Transmission_Pulley/hwcadj9-cable-adjuster.stp
CAD/Back_Transmission_Pulley/obmp-btp-1620.stp
CAD/Back_Transmission_Pulley/obmp-btp-1621.stp
CAD/Back_Transmission_Pulley/obmp-btp-1622.stp
CAD/Back_Transmission_Pulley/obmp-btp-1625.stp
CAD/Back_Transmission_Pulley/obmp-btp-1630.stp
CAD/Back_Transmission_Pulley/obmp-btp-1631.stp
CAD/Back_Transmission_Pulley/obmp-btp-1632.stp
CAD/Back_Transmission_Pulley/obmp-btp-1633.stp
CAD/Back_Transmission_Pulley/obmp-btp-1640.stp
CAD/Back_Transmission_Pulley/obmp-btp-1642.stp
CAD/Back_Transmission_Pulley/obmp-btp-1643.stp
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

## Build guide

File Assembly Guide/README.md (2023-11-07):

# Materials

## Components
The Bill_of_Materials.xlsx document contains the list of required components to assemble the bimanual robot. It also includes product numbers, prices and links to reseller webpages.
Most of the structure is designed to be 3D printed with reinforcing parts cut from carbon fibre plates. 
The original version was manufactured using the Prusa mk3 printers and standard filaments from Esun. Carbon fibre plates were cut using the desktop WAZER water jet cutter.
Some components are custom and require machining capabilities. These can be obtained from rapid prototyping services or from local machine shops. The BOM uses PCBWays for estimating the costs of the parts hence the price is more expensive than if the parts were locally printed. Additionally, the prices recorded are retail prices.
The BOM is organised with different pages for different modules :

* Bimanual_Robot_Arm_TypeA : The cost of building both arms, including the elbow and forearm rotation module TypeA (Power system not included)
* Stand : The base stand for the robot
* One_Unit_of_Forearm_ASL_Hand : Cost of building ONE ASL hand module
* One_Unit_of_Dynamixel_Hand : Cost of building ONE Dynamixel hand module
* One_Unit_of_Robotic_Wrist : Cost of building ONE Robotic wrist module
* Alternative_actuators : Miscellaneous items
* Power_supply : WIP

### WARNING: It is recommended to use the AMT102 series incremental encoders instead of the AMT232V absolute encoders
This is to make life easier without having to deal with noise in the SPI line. Otherwise a custom tristate buffer is required for correct operation of the encoder. (74AHC1G125S)

# Getting Started
## Things you will need
* Main computer (intel NUC7)
* DCHP router
* Raspberry pi 4
* Ethernet cables
  
## Multi-machine ROS setup
* Please follow the wiki for software setup
Connect the ethernet as depicted in the following diagram:
WIP
<p align="center">
  
</p>

goto your router dchp configuration page and reserve the IP for each machine using their MAC addresses
Setup ROS_IP and ROS_MASTER accordingly
link to ros multimachine tutorial page:

## ODriver Connection
The ODrive motor drivers can be connected directly to the BLDC motors and require a parallel CAN bus connection to the CANbus interface with the Raspberry Pi GPIO hat.
It is recommended to create a small connector hub for the connections for easier assembly and wire routing.
Motor power can be supplied directly from the battery but also from an isolated power supply. The following image shows the power schematic and the communication schematic of the system

WIP
<p align="center">
  
</p>

## Forearm Module Electronics

WIP

## Teleoperation controls

### Polhemus

### Captoglove

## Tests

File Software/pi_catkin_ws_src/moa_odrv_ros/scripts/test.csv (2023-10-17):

 | rh_wrist_flex | rh_wrist_piv | rh_wrist_rot | rh_thumb_meta | rh_thumb_piv | rh_index_dist | rh_index_meta | rh_index_piv | rh_middle_dist | rh_middle_meta | rh_middle_piv | rh_ring_dist | rh_ring_meta | rh_pinky_dist | rh_pinky_meta | ra_torso_bend | ra_flex | ra_abd | ra_rot | ra_elbow | lh_wrist_flex | lh_wrist_piv | lh_wrist_rot | lh_thumb_meta | lh_thumb_piv | lh_index_dist | lh_index_meta | lh_index_piv | lh_middle_dist | lh_middle_meta | lh_middle_piv | lh_ring_dist | lh_ring_meta | lh_pinky_dist | lh_pinky_meta | la_torso_bend | la_flex | la_abd | la_rot | la_elbow
0 | 0 | 0 | 0 | 0 | 0 | 0 | 0 | 0 | 0 | 0 | 0 | 0 | 0 | 0 | 0 | 0 | 0 | 0 | 0 | 0 | 0 | 0 | 0 | 0 | 0 | 0 | 0 | 0 | 0 | 0 | 0 | 0 | 0 | 0 | 0 | 0 | 0 | 0 | 0 | 0
1 | 0 | 0 | 0 | 0 | 0 | 0 | 0 | 0 | 0 | 0 | 0 | 0 | 0 | 0 | 0 | 0 | 0 | 0 | 0 | 0 | 0 | 0 | 0 | 0 | 0 | 0 | 0 | 0 | 0 | 0 | 0 | 0 | 0 | 0 | 0 | 0 | 0 | 0 | 0 | 0
2 | 0 | 0 | 0 | 0 | 0 | 0 | 0 | 0 | 0 | 0 | 0 | 0 | 0 | 0 | 0 | 0 | 0 | 0 | 0 | 0 | 0 | 0 | 0 | 0 | 0 | 0 | 0 | 0 | 0 | 0 | 0 | 0 | 0 | 0 | 0 | 0 | 0 | 0 | 0 | 0
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

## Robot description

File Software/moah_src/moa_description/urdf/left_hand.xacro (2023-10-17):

<?xml version="1.0"?>
<robot xmlns:xacro="http://www.ros.org/wiki/xacro" name="left_hand">
    <xacro:property name="thumb_diameter" value="0.02" />
    <xacro:property name="palm_size" value="0.09" />
    

<!-- finger_name = human/index -->
<!-- parent_link = human/left_palm -->
<!-- finger_diameter = 0.02 -->
<!-- meta_x = 0.03 -->
<!-- meta_y = 0.09 -->
<!-- prox_len = 0.04 -->
<!-- middle_len = 0.025 -->
<!-- distal_len = 0.02 -->

    <xacro:macro name="human_finger" params="finger_name parent_link finger_diameter meta_x meta_z prox_len middle_len distal_len piv_amplitude flex_amplitude">
        <link name="${finger_name}_meta"/>
        <link name="${finger_name}_proximal_0"/>
        <link name="${finger_name}_proximal_1">
            <visual>
                <origin rpy="0 0 0" xyz="0 0 ${prox_len/2}"/>
                <geometry>
                    <box size="${finger_diameter} ${finger_diameter} ${prox_len}"/>
                </geometry>
            </visual>
        </link>
        <link name="${finger_name}_middle">
            <visual>
                <origin rpy="0 0 0" xyz="0 0 ${middle_len/2}"/>
                <geometry>
                    <box size="${finger_diameter} ${finger_diameter} ${middle_len}"/>
                </geometry>
            </visual>
        </link>
        <link name="${finger_name}_distal">
            <visual>
                <origin rpy="0 0 0" xyz="0 0 ${distal_len/2}"/>
                <geometry>
                    <box size="${finger_diameter} ${finger_diameter} ${distal_len}"/>
                </geometry>
            </visual>
        </link>
        <link name="${finger_name}_tip"/>

        <joint name="${finger_name}_palm_meta" type="fixed">
            <origin rpy="0 0 0" xyz="${meta_x} 0 ${meta_z}"/>
            <parent link="${parent_link}"/>
            <child link="${finger_name}_meta"/>        
        </joint>

        <joint name="${finger_name}_meta_abdu" type="revolute">
            <origin rpy="0 0 0" xyz="0 0 0"/>
            <axis xyz="0 1 0"/>
            <parent link="${finger_name}_meta"/>
            <child link="${finger_name}_proximal_0"/>
            <limit effort="1" lower="-${piv_amplitude}" upper="${piv_amplitude}" velocity="1"/>
        </joint>

        <joint name="${finger_name}_meta_flex" type="revolute">
            <origin rpy="0 0 0" xyz="0 0 0"/>
            <axis xyz="-1 0 0"/>
            <parent link="${finger_name}_proximal_0"/>
            <child link="${finger_name}_proximal_1"/>
            <limit effort="1" lower="0" upper="${flex_amplitude}" velocity="1"/>
        </joint>

        <joint name="${finger_name}_proximal_flex" type="revolute">
            <origin rpy="0 0 0" xyz="0 0 ${prox_len}"/>
            <axis xyz="-1 0 0"/>
            <parent link="${finger_name}_proximal_1"/>
            <child link="${finger_name}_middle"/>
            <limit effort="1" lower="0" upper="${flex_amplitude}" velocity="1"/>
        </joint>

        <joint name="${finger_name}_middle_flex" type="revolute">
            <origin rpy="0 0 0" xyz="0 0 ${middle_len}"/>
            <axis xyz="-1 0 0"/>
            <parent link="${finger_name}_middle"/>
            <child link="${finger_name}_distal"/>
            <limit effort="1" lower="0" upper="${flex_amplitude}" velocity="1"/>
        </joint>

        <joint name="${finger_name}_tip_joint" type="fixed">
            <origin rpy="0 0 0" xyz="0 0 ${distal_len}"/>
            <parent link="${finger_name}_distal"/>
            <child link="${finger_name}_tip"/>            
        </joint>
    </xacro:macro>


    <link name="human/left_hand_mount"/>
    <link name="human/left_palm">
        <visual>
            <origin rpy="0 0 0" xyz="0 0 ${palm_size/2}"/>
            <geometry>
                <box size="${palm_size} ${thumb_diameter} ${palm_size}"/>
            </geometry>
        </visual>
    </link>

    <link name="human/left_hand_thumb_meta_0"/>
    <link name="human/left_hand_thumb_meta_1">
        <visual>
            <origin rpy="0 0 0" xyz="0.04 0 0"/>
            <geometry>
                <box size="0.08 ${thumb_diameter} ${thumb_diameter}"/>
            </geometry>
        </visual>
    </link>
    <link name="human/left_hand_thumb_prox">
        <visual>
            <origin rpy="0 0 0" xyz="${thumb_diameter} 0 0"/>
            <geometry>
                <box size="0.04 ${thumb_diameter} ${thumb_diameter}"/>
            </geometry>
        </visual>
    </link>
    <link name="human/left_hand_thumb_distal">
        <visual>
            <origin rpy="0 0 0" xyz="0.01 0 0"/>
            <geometry>
                <box size="0.02 ${thumb_diameter} ${thumb_diameter}"/>
            </geometry>
        </visual>
    </link>

    <link name="human/left_hand_thumb_tip"/>

    <!-- Joints -->
    <joint name="left_hand_mount2palm" type="fixed">
        <origin rpy="0 0 ${pi}" xyz="0 0 0"/>
        <parent link="human/left_hand_mount"/>
        <child link="human/left_palm"/>
    </joint>
    <!-- Thumb -->

    <joint name="left_hand/thumb_meta_abdu" type="revolute">
        <origin rpy="0 0 0" xyz="0 0 0"/>
        <axis xyz="0 -1 0"/>
        <parent link="human/left_palm"/>
        <child link="human/left_hand_thumb_meta_0"/>
        <limit effort="1" lower="0" upper="${pi/2}" velocity="1"/>
    </joint>

    <joint name="left_hand/thumb_meta_flex" type="revolute">
        <origin rpy="0 0 0" xyz="0 0 0.07"/>
        <axis xyz="0 0 1"/>
        <parent link="human/left_hand_thumb_meta_0"/>
        <child link="human/left_hand_thumb_meta_1"/>
        <limit effort="1" lower="0" upper="${pi/2}" velocity="1"/>
    </joint>
    
    <joint name="left_hand/thumb_proximal_flex" type="revolute">
        <origin rpy="0 0 0" xyz="0.08 0 0"/>
        <axis xyz="0 -1 0"/>
        <parent link="human/left_hand_thumb_meta_1"/>
        <child link="human/left_hand_thumb_prox"/>
        <limit effort="1" lower="0" upper="${pi/2}" velocity="1"/>
    </joint>

    <joint name="left_hand/thumb_distal_flex" type="revolute">
        <origin rpy="0 0 0" xyz="0.04 0 0"/>
        <axis xyz="0 -1 0"/>
        <parent link="human/left_hand_thumb_prox"/>
        <child link="human/left_hand_thumb_distal"/>
        <limit effort="1" lower="0" upper="${pi/2}" velocity="1"/>
    </joint>

    <joint name="left_thumb_tip_joint" type="fixed">
        <origin rpy="0 0 0" xyz="0.02 0 0"/>        
        <parent link="human/left_hand_thumb_distal"/>
        <child link="human/left_hand_thumb_tip"/>        
    </joint>


<!-- finger_name = human/index -->
<!-- parent_link = human/left_palm -->
<!-- finger_diameter = 0.02 -->
<!-- meta_x = 0.03 -->
<!-- meta_y = 0.09 -->
<!-- prox_len = 0.04 -->
<!-- middle_len = 0.025 -->
<!-- distal_len = 0.02 -->

    <!-- <xacro:macro name="human_finger" params="finger_name parent_link finger_diameter meta_x meta_z prox_len middle_len distal_len"> -->

    <xacro:human_finger finger_name="left_hand/index" parent_link="human/left_palm" finger_diameter="0.02" meta_x="0.03" meta_z="0.09" prox_len="0.04" middle_len="0.025" distal_len="0.02" piv_amplitude="${pi/4}" flex_amplitude="${pi/2}"/>
    <xacro:human_finger finger_name="left_hand/middle" parent_link="human/left_palm" finger_diameter="0.02" meta_x="0.01" meta_z="0.09" prox_len="0.05" middle_len="0.03" distal_len="0.02" piv_amplitude="${pi/4}" flex_amplitude="${pi/2}"/>
    <xacro:human_finger finger_name="left_hand/ring" parent_link="human/left_palm" finger_diameter="0.02" meta_x="-0.01" meta_z="0.09" prox_len="0.04" middle_len="0.025" distal_len="0.02" piv_amplitude="${pi/4}" flex_amplitude="${pi/2}"/>
    <xacro:human_finger finger_name="left_hand/pinky" parent_link="human/left_palm" finger_diameter="0.02" meta_x="-0.03" meta_z="0.08" prox_len="0.04" middle_len="0.02" distal_len="0.02" piv_amplitude="${pi/4}" flex_amplitude="${pi/2}"/>
</robot>

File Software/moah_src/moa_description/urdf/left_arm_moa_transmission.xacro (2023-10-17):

<?xml version="1.0"?>
<robot name="human_left_arm" xmlns:xacro="http://www.ros.org/wiki/xacro">

  <xacro:macro name="left_arm" params="">

    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
    <link name="human/left_arm_mount"/>

    <link name="human/left_arm_ref_frame">  
      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
    </link>
    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
    <link name="human/left_arm_frame0">
      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
    </link>
    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
    <link name="human/left_arm_frame1">
      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
    </link>
    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
    <link name="human/left_arm_frame2">
      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
    </link>
    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
    <link name="human/left_arm_frame3">
      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

    </link>
    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
    <link name="human/left_arm_frame4">
      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

    </link>
    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
    <link name="human/left_arm_frame5">
      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

    </link>
    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
    <link name="human/left_arm_frame6">
      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
    </link>

    
    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
    <link name="human/left_arm_frame7"/>
    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
    <joint name="left_shoulder_ref_frame_joint" type="revolute">
      <origin rpy="0 ${-pi/2} 0" xyz="0.15 0 0"/>
      <parent link="human/left_arm_mount"/>
      <child link="human/left_arm_ref_frame"/>
      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
      <limit effort="1" lower="-0.5" upper="0.5" velocity="1"/>
    </joint>
    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



    <joint name="left_shoulder_1_flex_exte" type="revolute">
      <origin rpy="0 ${pi/2} 0" xyz="0.046 0 -0.18"/>
	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
      <axis xyz="-1 0 0"/>
      <parent link="human/left_arm_ref_frame"/>
      <child link="human/left_arm_frame0"/>
      <limit effort="1" lower="-1.57079632679" upper="2.35619449019" velocity="1"/>
    </joint>

    <joint name="left_shoulder_2_abdu_addu" type="revolute">
      <origin rpy="${-pi/2} 0 0" xyz="0.09 0 -0.05"/>
      <axis xyz="0 0 -1"/>
      <parent link="human/left_arm_frame0"/>
      <child link="human/left_arm_frame1"/>
      <limit effort="1" lower="-1.57079632679" upper="1.57079632679" velocity="1"/>
    </joint>

    <joint name="left_shoulder_3_rotation" type="revolute">
      <origin rpy="${pi/2} 0 0" xyz="0 0.16 0"/>
      <axis xyz="0 0 1"/>
      <parent link="human/left_arm_frame1"/>
      <child link="human/left_arm_frame2"/>
      <limit effort="1" lower="-1.57079632679" upper="1.57079632679" velocity="1"/>
    </joint>
    
    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
    <joint name="left_elbow_4_flex_exte" type="revolute">
      <origin rpy="0 0 0" xyz="0 -0.03 -0.228"/>
      <axis xyz="-1 0 0"/>
      <parent link="human/left_arm_frame2"/>
      <child link="human/left_arm_frame3"/>
      <limit effort="1" lower="0.0" upper="2.7925268" velocity="1"/>
    </joint>

    <joint name="left_wrist_5_abdu_addu" type="revolute">
      <origin rpy="0 0 0" xyz="0 0 0"/>
      <axis xyz="1 0 0"/>
      <parent link="human/left_arm_frame5"/>
      <child link="human/left_arm_frame6"/>
      <limit effort="1" lower="-0.78539816339" upper="0.78539816339" velocity="1"/>
    </joint>
    
    <joint name="left_wrist_6_flex_exte" type="revolute">
      <origin rpy="0 0 0" xyz="0 -0.003 -0.26389"/>
      <axis xyz="0 1 0"/>
      <parent link="human/left_arm_frame4"/>
      <child link="human/left_arm_frame5"/>
      <limit effort="1" lower="-1.57079632679" upper="1.57079632679" velocity="1"/>
    </joint>

    <joint name="left_7_prona_supin" type="revolute">
      <origin rpy="0 0 ${pi}" xyz="0 0.03 -0.11951"/>
      <axis xyz="0 0 1"/>
      <parent link="human/left_arm_frame3"/>
      <child link="human/left_arm_frame4"/>
      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
      <limit effort="1" lower="-${pi}" upper="${pi}" velocity="1"/>
    </joint>

    <joint name="left_wrist_hand" type="fixed">
      <origin rpy="${pi} 0 ${pi/2}" xyz="0 0 0"/>
      <parent link="human/left_arm_frame6"/>
      <child link="human/left_arm_frame7"/>
    </joint>

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
  </xacro:macro>

</robot>

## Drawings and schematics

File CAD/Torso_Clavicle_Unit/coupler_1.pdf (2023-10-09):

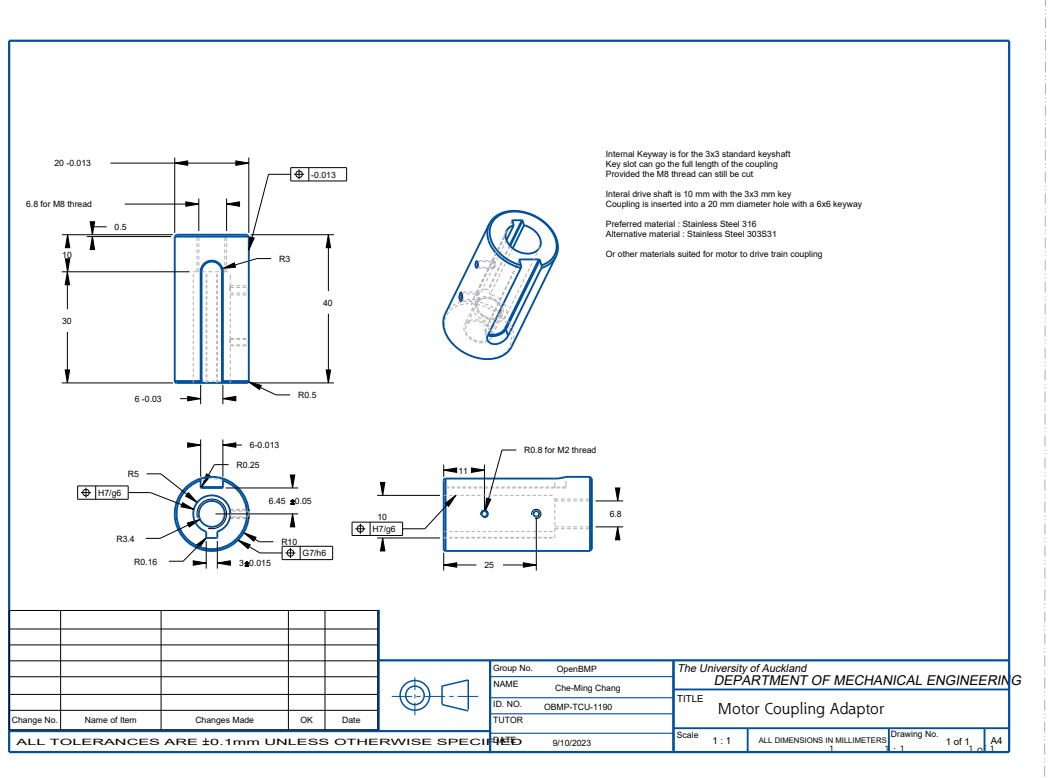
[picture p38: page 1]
NAME; ID. NO. TUTOR; DATE; Scale; ALL DIMENSIONS IN MILLIMETERS; A4 Drawing No. 1 : 1; Group No.; ALL TOLERANCES ARE; 0.1mm UNLESS OTHERWISE SPECIFIED; 6.8 for M8 thread; R0.8 for M2 thread; Change No.; Name of Item; Changes Made; Date

Internal Keyway is for the 3x3 standard keyshaft
Key slot can go the full length of the coupling
Provided the M8 thread can still be cut
Interal drive shaft is 10 mm with the 3x3 mm key
Coupling is inserted into a 20 mm diameter hole with a 6x6 keyway
Preferred material : Stainless Steel 316
Alternative material : Stainless Steel 303S31
Or other materials suited for motor to drive train coupling

OpenBMP
Che-Ming Chang
OBMP-TCU-1190

The University of Auckland
DEPARTMENT OF MECHANICAL ENGINEERING
TITLE
Motor Coupling Adaptor

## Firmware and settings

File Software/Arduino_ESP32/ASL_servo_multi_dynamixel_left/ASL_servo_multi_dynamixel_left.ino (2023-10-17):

#include <Dynamixel2Arduino.h>
#include <SoftwareSerial.h>
#include <ESP32Servo.h>
#include <ros.h>
#include <std_msgs/Float32MultiArray.h>

ros::NodeHandle  nh;

//Software serial for dynamixel - for rs485, remember to change Hardwareserial to softwareserial.
//SoftwareSerial (RX, TX)
//SoftwareSerial (RO, DI)
SoftwareSerial toRS485(34, 22);
const uint8_t DXL_DIR_PIN = 15; // DYNAMIXEL DIR PIN (RE/DE)

const uint8_t wristRot = 15;
const float DXL_PROTOCOL_VERSION = 2.0;

#define DXL_SERIAL   toRS485
#define DEBUG_SERIAL Serial

Dynamixel2Arduino dxl(DXL_SERIAL, DXL_DIR_PIN);


// create fourteen servo objects
Servo wristFlex;
Servo wristPiv;
//Servo wristRot;
Servo thumbMeta;
Servo thumbPiv;
Servo indexDis;
Servo indexMeta;
Servo indexPiv;
Servo middleDis;
Servo middleMeta;
Servo middlePiv;
Servo ringDis;
Servo ringMeta;
Servo pinkyDis;
Servo pinkyMeta;

Servo elbowLockA;
Servo elbowLockB;

int minUs = 500;
int maxUs = 2500;
int steps = 0;
int pos = 0;      // position in degrees
ESP32PWM pwm;

void servo_cb( const std_msgs::Float32MultiArray& cmd_msg) {

  wristFlex.write(map(cmd_msg.data[0], -90, 10, 10, 165));
  wristPiv.write(map(cmd_msg.data[1], -25, 65, 20, 160));
  //wristRot.write(map(cmd_msg.data[2], -45, 200, 0, 180));
  // 0 = 3075 -90 = 2040 270 = 6250
  // -180 = 1000, 180 = 4100
  dxl.setGoalPosition(wristRot, map(cmd_msg.data[2], -180, 180, 1024, 5125));
  
  thumbMeta.write(map(cmd_msg.data[3], 0, 90, 10, 170));
  thumbPiv.write(map(cmd_msg.data[4], 0, 90, 30, 150));

  indexDis.write(map(cmd_msg.data[5], 0, 180, 10, 175));
  indexMeta.write(map(cmd_msg.data[6], 0, 90, 10, 175));

  indexPiv.write(map(cmd_msg.data[7], -10, 20, 10, 100));

  middleDis.write(map(cmd_msg.data[8], 0, 180, 10, 179));
  middleMeta.write(map(cmd_msg.data[9], 0, 90, 10, 179));
  
  middlePiv.write(map(cmd_msg.data[10], -45, 45, 30, 150));
  
  ringDis.write(map(cmd_msg.data[11], 0, 180, 10, 170));
  ringMeta.write(map(cmd_msg.data[12], 0, 90, 30, 179));

  pinkyDis.write(map(cmd_msg.data[13], 0, 180, 10, 150));
  pinkyMeta.write(map(cmd_msg.data[14], 0, 90, 10, 170));

  /*if(cmd_msg.data[15] > 50)
  { //lock
    //elbowLockA.write(map(cmd_msg.data[15], 0, 1, 20, 50));
    //elbowLockB.write(map(cmd_msg.data[15], 0, 1, 150, 100));
    elbowLockA.write(20);
    elbowLockB.write(150);
  }
  else
  {//unlocked
    elbowLockA.write(50);
    elbowLockB.write(100);
  }
  */
}

ros::Subscriber<std_msgs::Float32MultiArray> sub("leftservo", servo_cb);


void setup() {
  /***************************************************************
    Dynamixel communication and servo setup
  ***************************************************************/
  // comment out serial monitor when done:
  Serial.begin(115200);
  nh.getHardware()->setBaud(115200);
  // Set Port baudrate to 57600bps. This has to match with DYNAMIXEL baudrate.
  dxl.begin(57600);
  // Set Port Protocol Version. This has to match with DYNAMIXEL protocol version.
  dxl.setPortProtocolVersion(DXL_PROTOCOL_VERSION);
  // Get DYNAMIXEL information
  dxl.ping(wristRot);
  dxl.torqueOff(wristRot);
  dxl.setOperatingMode(wristRot, OP_CURRENT_BASED_POSITION);
  dxl.torqueOn(wristRot);
  dxl.setGoalPosition(wristRot, 3075);

  /***************************************************************
    ESP32 Servo setup
  ***************************************************************/

  ESP32PWM::allocateTimer(0);
  ESP32PWM::allocateTimer(1);
  ESP32PWM::allocateTimer(2);
  ESP32PWM::allocateTimer(3);

  //  wristFlex.setPeriodHertz(49.8);
  //  wristPiv.setPeriodHertz(50);
  //  wristRot.setPeriodHertz(50);
  //  thumbMeta.setPeriodHertz(50);
  //  thumbPiv.setPeriodHertz(50);
  //  indexDis.setPeriodHertz(50);
  //  indexMeta.setPeriodHertz(50);
  //  indexPiv.setPeriodHertz(50);
  //  middleDis.setPeriodHertz(50);
  //  middleMeta.setPeriodHertz(49.8);
  //  middlePiv.setPeriodHertz(50);
  //  ringDis.setPeriodHertz(50);
  //  ringMeta.setPeriodHertz(50);
  //  pinkyDis.setPeriodHertz(50);
  //  pinkyMeta.setPeriodHertz(50);

  //servo1.setPeriodHertz(50);      // Standard 50hz servo
  //servo2.setPeriodHertz(50);      // Standard 50hz servo
  //servo3.setPeriodHertz(330);      // Standard 50hz servo
  //servo4.setPeriodHertz(200);      // Standard 50hz servo
  //servo5.setPeriodHertz(50);      // Standard 50hz servo

  wristFlex.attach(33, minUs, maxUs);
  wristPiv.attach(32, minUs, maxUs);
  //wristRot.attach(, minUs, maxUs);
  thumbMeta.attach(2, minUs, maxUs);
  thumbPiv.attach(27, minUs, maxUs);
  indexDis.attach(14, minUs, maxUs);
  indexMeta.attach(4, minUs, maxUs);
  indexPiv.attach(12, minUs, maxUs);
  middleDis.attach(26, minUs, maxUs);
  middleMeta.attach(17, minUs, maxUs);
  middlePiv.attach(18, minUs, maxUs);
  ringDis.attach(25, minUs, maxUs);
  ringMeta.attach(16, minUs, maxUs);
  pinkyDis.attach(21, minUs, maxUs);
  pinkyMeta.attach(19, minUs, maxUs);

  
  elbowLockA.attach(23);
  elbowLockB.attach(13);
  /***************************************************************
    Rosnode setup
  ***************************************************************/
  nh.initNode();
  nh.subscribe(sub);


}

void loop() {
  nh.spinOnce();
  delay(1);
}

int map(float x, float in_min, float in_max, float out_min, float out_max) {
  if (x > in_max)
  {
    return out_max;
  }
  else if (x < in_min)
  {
    return out_min;
  }
  else
  {
    return (x - in_min) * (out_max - out_min) / (in_max - in_min) + out_min;
  }
}

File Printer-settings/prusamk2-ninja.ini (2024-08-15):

[filament:NinjaTek NinjaFlex TPU Black]
bed_temperature = 50
bridge_fan_speed = 100
compatible_printers = 
compatible_printers_condition = nozzle_diameter[0]>0.35 and printer_model!="MK2SMM" 
and printer_model!="MINI" and printer_notes!~/.*PG.*/ 
and num_extruders==1 && ! (printer_notes=~/.*PRINTER_VENDOR_PRUSA3D.*/
and printer_notes=~/.*PRINTER_MODEL_MK3.*/ 
and single_extruder_multi_material)
compatible_prints = 
compatible_prints_condition = 
cooling = 1
disable_fan_first_layers = 1
enable_dynamic_fan_speeds = 0
end_filament_gcode = "; Filament-specific end gcode"
extrusion_multiplier = 1.2
fan_always_on = 1
fan_below_layer_time = 100
filament_colour = #353535
filament_cooling_final_speed = 3.4
filament_cooling_initial_speed = 2.2
filament_cooling_moves = 4
filament_cost = 85
filament_density = 1.19
filament_deretract_speed = 25
filament_diameter = 1.75
filament_load_time = 0
filament_loading_speed = 28
filament_loading_speed_start = 3
filament_max_volumetric_speed = 1.2
filament_minimal_purge_on_wipe_tower = 15
filament_multitool_ramming = 0
filament_multitool_ramming_flow = 10
filament_multitool_ramming_volume = 10
filament_notes = ""
filament_purge_multiplier = 100%
filament_ramming_parameters = "120 100 6.6 6.8 7.2 7.6 7.9 8.2 8.7 9.4 9.9 10.0 |
0.05 6.6 0.45 6.8 0.95 7.8 1.45 8.3 1.95 9.7 2.45 10 2.95 7.6 3.45 7.6 3.95 7.6 4.45 7.6 4.95 7.6"
filament_retract_before_travel = 3
filament_retract_before_wipe = nil
filament_retract_layer_change = nil
filament_retract_length = 2.5
filament_retract_length_toolchange = nil
filament_retract_lift = 0
filament_retract_lift_above = nil
filament_retract_lift_below = nil
filament_retract_restart_extra = nil
filament_retract_restart_extra_toolchange = nil
filament_retract_speed = 60
filament_settings_id = ""
filament_soluble = 0
filament_spool_weight = 0
filament_stamping_distance = 0
filament_stamping_loading_speed = 20
filament_toolchange_delay = 0
filament_travel_lift_before_obstacle = nil
filament_travel_max_lift = nil
filament_travel_ramping_lift = nil
filament_travel_slope = nil
filament_type = FLEX
filament_unload_time = 0
filament_unloading_speed = 90
filament_unloading_speed_start = 100
filament_vendor = NinjaTek
filament_wipe = 0
first_layer_bed_temperature = 50
first_layer_temperature = 240
full_fan_speed_layer = 3
idle_temperature = nil
inherits = NinjaTek NinjaFlex TPU
max_fan_speed = 100
min_fan_speed = 60
min_print_speed = 10
overhang_fan_speed_0 = 0
overhang_fan_speed_1 = 0
overhang_fan_speed_2 = 0
overhang_fan_speed_3 = 0
slowdown_below_layer_time = 10
start_filament_gcode = "M900 K0 ; Filament gcode"
temperature = 235
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

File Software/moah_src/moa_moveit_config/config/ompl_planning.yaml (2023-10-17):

planner_configs:
  AnytimePathShortening:
    type: geometric::AnytimePathShortening
    shortcut: true  # Attempt to shortcut all new solution paths
    hybridize: true  # Compute hybrid solution trajectories
    max_hybrid_paths: 24  # Number of hybrid paths generated per iteration
    num_planners: 4  # The number of default planners to use for planning
    planners: ""  # A comma-separated list of planner types (e.g., "PRM,EST,RRTConnect"Optionally, planner parameters can be passed to change the default:"PRM[max_nearest_neighbors=5],EST[goal_bias=.5],RRT[range=10. goal_bias=.1]"
  SBL:
    type: geometric::SBL
    range: 0.0  # Max motion added to tree. ==> maxDistance_ default: 0.0, if 0.0, set on setup()
  EST:
    type: geometric::EST
    range: 0.0  # Max motion added to tree. ==> maxDistance_ default: 0.0, if 0.0 setup()
    goal_bias: 0.05  # When close to goal select goal, with this probability. default: 0.05
  LBKPIECE:
    type: geometric::LBKPIECE
    range: 0.0  # Max motion added to tree. ==> maxDistance_ default: 0.0, if 0.0, set on setup()
    border_fraction: 0.9  # Fraction of time focused on boarder default: 0.9
    min_valid_path_fraction: 0.5  # Accept partially valid moves above fraction. default: 0.5
  BKPIECE:
    type: geometric::BKPIECE
    range: 0.0  # Max motion added to tree. ==> maxDistance_ default: 0.0, if 0.0, set on setup()
    border_fraction: 0.9  # Fraction of time focused on boarder default: 0.9
    failed_expansion_score_factor: 0.5  # When extending motion fails, scale score by factor. default: 0.5
    min_valid_path_fraction: 0.5  # Accept partially valid moves above fraction. default: 0.5
  KPIECE:
    type: geometric::KPIECE
    range: 0.0  # Max motion added to tree. ==> maxDistance_ default: 0.0, if 0.0, set on setup()
    goal_bias: 0.05  # When close to goal select goal, with this probability. default: 0.05
    border_fraction: 0.9  # Fraction of time focused on boarder default: 0.9 (0.0,1.]
    failed_expansion_score_factor: 0.5  # When extending motion fails, scale score by factor. default: 0.5
    min_valid_path_fraction: 0.5  # Accept partially valid moves above fraction. default: 0.5
  RRT:
    type: geometric::RRT
    range: 0.0  # Max motion added to tree. ==> maxDistance_ default: 0.0, if 0.0, set on setup()
    goal_bias: 0.05  # When close to goal select goal, with this probability? default: 0.05
  RRTConnect:
    type: geometric::RRTConnect
    range: 0.0  # Max motion added to tree. ==> maxDistance_ default: 0.0, if 0.0, set on setup()
  RRTstar:
    type: geometric::RRTstar
    range: 0.0  # Max motion added to tree. ==> maxDistance_ default: 0.0, if 0.0, set on setup()
    goal_bias: 0.05  # When close to goal select goal, with this probability? default: 0.05
    delay_collision_checking: 1  # Stop collision checking as soon as C-free parent found. default 1
  TRRT:
    type: geometric::TRRT
    range: 0.0  # Max motion added to tree. ==> maxDistance_ default: 0.0, if 0.0, set on setup()
    goal_bias: 0.05  # When close to goal select goal, with this probability? default: 0.05
    max_states_failed: 10  # when to start increasing temp. default: 10
    temp_change_factor: 2.0  # how much to increase or decrease temp. default: 2.0
    min_temperature: 10e-10  # lower limit of temp change. default: 10e-10
    init_temperature: 10e-6  # initial temperature. default: 10e-6
    frountier_threshold: 0.0  # dist new state to nearest neighbor to disqualify as frontier. default: 0.0 set in setup()
    frountierNodeRatio: 0.1  # 1/10, or 1 nonfrontier for every 10 frontier. default: 0.1
    k_constant: 0.0  # value used to normalize expresssion. default: 0.0 set in setup()
  PRM:
    type: geometric::PRM
    max_nearest_neighbors: 10  # use k nearest neighbors. default: 10
  PRMstar:
    type: geometric::PRMstar
  FMT:
    type: geometric::FMT
    num_samples: 1000  # number of states that the planner should sample. default: 1000
    radius_multiplier: 1.1  # multiplier used for the nearest neighbors search radius. default: 1.1
    nearest_k: 1  # use Knearest strategy. default: 1
    cache_cc: 1  # use collision checking cache. default: 1
    heuristics: 0  # activate cost to go heuristics. default: 0
    extended_fmt: 1  # activate the extended FMT*: adding new samples if planner does not finish successfully. default: 1
  BFMT:
    type: geometric::BFMT
    num_samples: 1000  # number of states that the planner should sample. default: 1000
    radius_multiplier: 1.0  # multiplier used for the nearest neighbors search radius. default: 1.0
    nearest_k: 1  # use the Knearest strategy. default: 1
    balanced: 0  # exploration strategy: balanced true expands one tree every iteration. False will select the tree with lowest maximum cost to go. default: 1
    optimality: 1  # termination strategy: optimality true finishes when the best possible path is found. Otherwise, the algorithm will finish when the first feasible path is found. default: 1
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

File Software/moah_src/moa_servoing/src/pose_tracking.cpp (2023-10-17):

/*******************************************************************************
 *      Title     : pose_tracking_example.cpp
 *      Project   : moveit_servo
 *      Created   : 09/04/2020
 *      Author    : Adam Pettinger
 *
 * BSD 3-Clause License
 *
 * Copyright (c) 2019, Los Alamos National Security, LLC
 * All rights reserved.
 *
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
 * * Neither the name of the copyright holder nor the names of its
 *   contributors may be used to endorse or promote products derived from
 *   this software without specific prior written permission.
 *
 * THIS SOFTWARE IS PROVIDED BY THE COPYRIGHT HOLDERS AND CONTRIBUTORS "AS IS"
 * AND ANY EXPRESS OR IMPLIED WARRANTIES, INCLUDING, BUT NOT LIMITED TO, THE
 * IMPLIED WARRANTIES OF MERCHANTABILITY AND FITNESS FOR A PARTICULAR PURPOSE
 * ARE
 * DISCLAIMED. IN NO EVENT SHALL THE COPYRIGHT HOLDER OR CONTRIBUTORS BE LIABLE
 * FOR ANY DIRECT, INDIRECT, INCIDENTAL, SPECIAL, EXEMPLARY, OR CONSEQUENTIAL
 * DAMAGES (INCLUDING, BUT NOT LIMITED TO, PROCUREMENT OF SUBSTITUTE GOODS OR
 * SERVICES; LOSS OF USE, DATA, OR PROFITS; OR BUSINESS INTERRUPTION) HOWEVER
 * CAUSED AND ON ANY THEORY OF LIABILITY, WHETHER IN CONTRACT, STRICT LIABILITY,
 * OR TORT (INCLUDING NEGLIGENCE OR OTHERWISE) ARISING IN ANY WAY OUT OF THE USE
 * OF THIS SOFTWARE, EVEN IF ADVISED OF THE POSSIBILITY OF SUCH DAMAGE.
 *******************************************************************************/

#include <geometry_msgs/TransformStamped.h>
#include <moveit_servo/make_shared_from_pool.h>
#include <moveit_servo/pose_tracking.h>
#include <moveit_servo/servo.h>
#include <moveit_servo/status_codes.h>
#include <std_msgs/Int8.h>

#include <thread>

static const std::string LOGNAME = "cpp_interface_example";

// Class for monitoring status of moveit_servo
class StatusMonitor {
   public:
    StatusMonitor(ros::NodeHandle& nh, const std::string& topic) {
        sub_ = nh.subscribe(topic, 1, &StatusMonitor::statusCB, this);
    }

   private:
    void statusCB(const std_msgs::Int8ConstPtr& msg) {
        moveit_servo::StatusCode latest_status = static_cast<moveit_servo::StatusCode>(msg->data);
        if (latest_status != status_) {
            status_ = latest_status;
            const auto& status_str = moveit_servo::SERVO_STATUS_CODE_MAP.at(status_);
            ROS_INFO_STREAM_NAMED(LOGNAME, "Servo status: " << status_str);
        }
    }
    moveit_servo::StatusCode status_ = moveit_servo::StatusCode::INVALID;
    ros::Subscriber sub_;
};

/**
 * Instantiate the pose tracking interface.
 * Send a pose slightly different from the starting pose
 * Then keep updating the target pose a little bit
 */
int main(int argc, char** argv) {
    ros::init(argc, argv, LOGNAME);
    ros::NodeHandle nh("~");
    ros::AsyncSpinner spinner(8);
    spinner.start();

    // Load the planning scene monitor
    planning_scene_monitor::PlanningSceneMonitorPtr planning_scene_monitor;
    planning_scene_monitor =
        std::make_shared<planning_scene_monitor::PlanningSceneMonitor>("robot_description");
    if (!planning_scene_monitor->getPlanningScene()) {
        ROS_ERROR_STREAM_NAMED(LOGNAME, "Error in setting up the PlanningSceneMonitor.");
        exit(EXIT_FAILURE);
    }

    planning_scene_monitor->startSceneMonitor();
    planning_scene_monitor->startWorldGeometryMonitor(
        planning_scene_monitor::PlanningSceneMonitor::DEFAULT_COLLISION_OBJECT_TOPIC,
        planning_scene_monitor::PlanningSceneMonitor::DEFAULT_PLANNING_SCENE_WORLD_TOPIC,
        false /* skip octomap monitor */);
    planning_scene_monitor->startStateMonitor();

    // Create the pose tracker
    moveit_servo::PoseTracking tracker(nh, planning_scene_monitor);

    // Make a publisher for sending pose commands
    // ros::Publisher target_pose_pub =
    //     nh.advertise<geometry_msgs::PoseStamped>("target_pose", 1 /* queue */, true /* latch */);

    // Subscribe to servo status (and log it when it changes)
    StatusMonitor status_monitor(nh, "status");

    Eigen::Vector3d lin_tol{0.0, 0.0, 0.0};
    double rot_tol = 0.0;

    // resetTargetPose() can be used to clear the target pose and wait for a new one, e.g. when
    // moving between multiple waypoints
    tracker.resetTargetPose();

    // Publish target pose
    // target_pose.header.stamp = ros::Time::now();
    // target_pose_pub.publish(target_pose);

    // Run the pose tracking in a new thread
    ros::Rate loop_rate(1000);
    while (ros::ok()) {
        tracker.moveToPose(lin_tol, rot_tol, 0.005 /* target pose timeout */);
        ros::spinOnce();
        loop_rate.sleep();
    }

    // Make sure the tracker is stopped and clean up
    tracker.stopMotion();

    return EXIT_SUCCESS;
}

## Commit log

2023-10-17 Initial software commit
    [base_xacros.xacro, both_hands.csv, dual_arm.xacro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]
2024-04-18 Delete Software/pi_catkin_ws_src/catkin_ws/src/odrive_ros directory
    removed old version to condense to working version. removed old place holder readme files
2024-05-26 Add files via upload
    repaired part 1143 for heat insert size
    [obmp-tcu-1143.stp]
2024-08-27 Add files via upload
    Solid versions of the upper and lower plates (without servo)
    [OBMP-TCU-1160-S.stp, OBMP-TCU-1170-S.stp]
